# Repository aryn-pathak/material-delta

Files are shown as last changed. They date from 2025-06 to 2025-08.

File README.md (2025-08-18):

# MATERIAL DELTA (stylised as mδ)
## Concept:
**"What if a printer was 3D printed?"** _thats called a reprap printer, nothing new, duh!_

**"Alright, what if it was super cheap, about $150?"** _Impressive, but it's probably super small, super slow, and super low quality too. why not splurge the $350 limit you have!_

**"Nope, what if it was ultra fast too?"** _powerful motors and a 100W hotend, nothing special either-- probably eats up a TON of power!_

**"Can't you ever be happy?! Fine, what if it was powered by USBC?"** _you're kidding thats not possible blah blah blah about how a 3D printer can't be powered by USBC_

The Material DELTA is an opensource delta style 3D printer, built for speed, pockets, and powered by USBC, powered by a RPi Zero 2W running klipper, with raspberry pi pico controlling motors for high speed motion.

## images (they're beautiful)






# BOM:

| Category | Name | Link | Price (INR) | Price (USD) |
|---|---|---|---|---|
| CONTROLLER PARTS | NCE4080K | [Link](https://roboticsdna.in/product/nce4080k-40v-80a-n-channel-enhancement-mode-power-mosfet/) | 108 | 1.296 |
| | PDC004-PD | [Link](https://robu.in/product/pdc004-pd-pd-decoy-module-20v/) | 109 | 1.308 |
| | SMBJ6.0A | [Link](https://roboticsdna.in/product/smbj6-0a-6v-600w-esd-suppressor-tvs-diode-2pin-smb-do-214aa/) | 20 | 0.24 |
| | 100uF 25V Electrolytic Capacitor | [Link](https://robu.in/product/100uf-25v-electrolytic-capacitor-pack-of-10/) | 6 | 0.072 |
| | 1N5819 | [Link](https://roboticsdna.in/product/in5819-schottky-diode/) | 61 | 0.732 |
| | Connector (x2) | [Link](https://roboticsdna.in/product/xy2500-9-pin-3-81-mm-male-pitch-straight-screw-terminal-block-socket/) | 391 | 4.692 |
| | Orpheus Pico | available @ home | 0 | 0 |
| | RPi Zero 2W | available @ home | 0 | 0 |
| | TMC2226 Stepper driver (x4) | [Link](https://novo3d.in/tmc2226-driver/) | 1796 | 21.552 |
| | XL4015 Step down | [Link](https://robu.in/product/xl4015-5a-dc-dc-step-down-adjustable-power-supply-buck-module-led-with-heatsink/) | 75 | 0.9 |
| | XL6019E1 Step up | [Link](https://robu.in/product/xl6019e1-dc-dc-step-converter-performance-ultra-lm2577-booster-circuit-board/) | 155 | 1.86 |
| PRINTER PARTS | Nema 17 (x4) | [Link](https://novo3d.in/42-stepper-motor-nema17/) | 2316 | 27.792 |
| | Volcano heatblock | [Link](https://novo3d.in/pt100-volcano-heat-block/) | 149 | 1.788 |
| | Heater | [Link](https://novo3d.in/24v-50w-heater-cartridge/) | 99 | 1.188 |
| | Heatbreak | [Link](https://novo3d.in/ender3-s1-sprite-throat/) | 169 | 2.028 |
| | CHT Nozzle (0.6mm) | [Link](https://novo3d.in/v6-cht-nozzle/) | 129 | 1.548 |
| | Heatsink | [Link](https://novo3d.in/e3d-v6-heatsink/) | 79 | 0.948 |
| | 3010 Fan | [Link](https://robu.in/product/12v-3010-cooling-fan-for-3d-printer/) | 71 | 0.852 |
| | Pneumatic connector | [Link](https://novo3d.in/pc4-m6/) | 20 | 0.24 |
| | Tube (x2) | [Link](https://novo3d.in/ptfe-tube-white/) | 218 | 2.616 |
| | 2020 extrusions (5m) | [Link](https://www.fastdep.in/product/tslot-2020/?src=search&q=2020) | 1895 | 22.74 |
| | Titan extruder | [Link](https://novo3d.in/titan-extruder/) | 399 | 4.788 |
| | Ball joints for arms | [Link](https://roboticsdna.in/product/reprap-delta-kossel-mini-5347-delta-ball-headed-buckle-ball-caps-parallel-arm-rod-carbon-rod-joints-kit-with-12pcs-m3-for-3d-printer/) | 400 | 4.8 |
| | Carbon fiber arms (x2) | [Link]([https://robu.in/product/pultruded-carbon-fiber-tube-hollow-3mmod-1-5mm-id-1000mm-pack-of-2/](https://robu.in/product/pultruded-carbon-fiber-tube-hollow-6mm-4mm-500mm-pack-of-2/)) | 642 | 7.51 |
| | GT2 timing pulley (x3) | [Link](https://novo3d.in/motor-pulley/) | 75 | 0.9 |
| | Idler pulley | [Link](https://novo3d.in/idler-pulley-6mm/) | 65 | 0.78 |
| | GT2 timing belt | [Link](https://novo3d.in/gt2-6mm-belt/) | 120 | 1.44 |
| | V Slot wheels (x9) | [Link](https://novo3d.in/v-wheel/) | 1071 | 12.852 |
| | 2040 extrusion (3m) | [Link](https://www.fastdep.in/product/tslot-vslot-2040/?src=search&q=2040%2520extrusions) | 2646 | 31.752 |
| | 5010 blower | [Link](https://novo3d.in/blower-cooling-fan-5015/) | 75 | 0.9 |
| | Thermistor | [Link](https://novo3d.in/ntc-sensor/) | 99 | 1.188 |
| | 1kg PLA | [Link](https://novo3d.in/filament/) | 799 | 9.588 |
| | 10mm Spiral Wrapping | [Link](https://robu.in/product/10mm-spiral-wrapping-band-black-10m-for-wires/) | 90 | 1.08 |
| | Round bed sticker | [Link](https://robu.in/product/round-heated-bed-sticker-for-3d-printer-build-plate-with-adhesive-backing/) | 274 | 3.288 |
| | PVC tape | [Link](https://robu.in/product/pro-power-pvc-tape-1920b-general-purpose-tape-pvc-20m-x-19mm/) | 167 | 2.004 |
| | Endstop switches (x6) | [Link](https://roboticsdna.in/product/omron-3d-printer-limit-switch-endstop-ss-5gl/) | 240 | 2.88 |
| FASTENERS | M3 x 12mm | [Link](https://www.fastdep.in/product/socket-head-m3x12mm/) | 26 | 0.312 |
| | M3 x 25mm (x2) | [Link](https://www.fastdep.in/product/socket-head-screws-m3x25mm/) | 60 | 0.72 |
| | M5 x 10mm (x5) | [Link](https://www.fastdep.in/product/socket-head-screws-m5x10mm/) | 140 | 1.68 |
| | M3 Hex Nut | [Link](https://www.fastdep.in/product/hex-nut-m3/) | 18 | 0.216 |
| | M5 hammernut (x50) | [Link](https://novo3d.in/hammernut/) | 300 | 3.6 |
| | M2.5 x 8mm | [Link](https://www.fastdep.in/product/pan-head-screw-m2-5x8mm/) | 48 | 0.576 |
| **TOTAL** | | | **₹15500**  | **$186** |

Huge huge huge thanks to Hack Club and for making this possible :D

# EDITS
- Made new duct, with clearance and pointing right below the nozzle (instead of on it)



- Made it taller for more Z axis
- Added bowden mount for extruder
- Added filament holder



- Modelled in the boards



- Fixed duct based on feedback from reviewers!


- Made new filament holder


- Added belt tensioners!


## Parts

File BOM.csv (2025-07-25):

Category | Name | Link | Price (INR) | Price (USD)
CONTROLLER PARTS | NCE4080K | https://roboticsdna.in/product/nce4080k-40v-80a-n-channel-enhancement-mode-power-mosfet/ | 108 | 1.296
 | PDC004-PD | https://robu.in/product/pdc004-pd-pd-decoy-module-20v/ | 109 | 1.308
 | SMBJ6.0A | https://roboticsdna.in/product/smbj6-0a-6v-600w-esd-suppressor-tvs-diode-2pin-smb-do-214aa/ | 20 | 0.24
 | 100uF 25V Electrolytic Capacitor | https://robu.in/product/100uf-25v-electrolytic-capacitor-pack-of-10/ | 6 | 0.072
 | 1N5819 | https://roboticsdna.in/product/in5819-schottky-diode/ | 61 | 0.732
 | Connector (x2) | https://roboticsdna.in/product/xy2500-9-pin-3-81-mm-male-pitch-straight-screw-terminal-block-socket/ | 391 | 4.692
 | Orpheus Pico | available @ home | 0 | 0
 | RPi Zero 2W | available @ home | 0 | 0
 | TMC2226 Stepper driver (x4) | https://novo3d.in/tmc2226-driver/ | 1796 | 21.552
 | XL4015 Step down | https://robu.in/product/xl4015-5a-dc-dc-step-down-adjustable-power-supply-buck-module-led-with-heatsink/ | 75 | 0.9
 | XL6019E1 Step up | https://robu.in/product/xl6019e1-dc-dc-step-converter-performance-ultra-lm2577-booster-circuit-board/ | 155 | 1.86
PRINTER PARTS | Nema 17 (x4) | https://novo3d.in/42-stepper-motor-nema17/ | 2316 | 27.792
 | Volcano heatblock | https://novo3d.in/pt100-volcano-heat-block/ | 149 | 1.788
 | Heater | https://novo3d.in/24v-50w-heater-cartridge/ | 99 | 1.188
 | Heatbreak | https://novo3d.in/ender3-s1-sprite-throat/ | 169 | 2.028
 | CHT Nozzle (0.6mm) | https://novo3d.in/v6-cht-nozzle/ | 129 | 1.548
 | Heatsink | https://novo3d.in/e3d-v6-heatsink/ | 79 | 0.948
 | 3010 Fan | https://robu.in/product/12v-3010-cooling-fan-for-3d-printer/ | 71 | 0.852
 | Pneumatic connector | https://novo3d.in/pc4-m6/ | 20 | 0.24
 | Tube (x2) | https://novo3d.in/ptfe-tube-white/ | 218 | 2.616
 | 2020 extrusions (5m) | https://www.fastdep.in/product/tslot-2020/?src=search&q=2020 | 1895 | 22.74
 | Titan extruder | https://novo3d.in/titan-extruder/ | 399 | 4.788
 | Ball joints for arms | https://roboticsdna.in/product/reprap-delta-kossel-mini-5347-delta-ball-headed-buckle-ball-caps-parallel-arm-rod-carbon-rod-joints-kit-with-12pcs-m3-for-3d-pr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 | 400 | 4.8
 | Carbon fiber arms (x2) | https://robu.in/product/pultruded-carbon-fiber-tube-hollow-6mm-4mm-500mm-pack-of-2/ | 642 | 7.51
 | GT2 timing pulley (x3) | https://novo3d.in/motor-pulley/ | 75 | 0.9
 | Idler pulley | https://novo3d.in/idler-pulley-6mm/ | 65 | 0.78
 | GT2 timing belt | https://novo3d.in/gt2-6mm-belt/ | 120 | 1.44
 | V Slot wheels (x9) | https://novo3d.in/v-wheel/ | 1071 | 12.852
 | 2040 extrusion (3m) | https://www.fastdep.in/product/tslot-vslot-2040/?src=search&q=2040%2520extrusions | 2646 | 31.752
 | 5010 blower | https://novo3d.in/blower-cooling-fan-5015/ | 75 | 0.9
 | Thermistor | https://novo3d.in/ntc-sensor/ | 99 | 1.188
 | 1kg PLA | https://novo3d.in/filament/ | 799 | 9.588
 | 10mm Spiral Wrapping | https://robu.in/product/10mm-spiral-wrapping-band-black-10m-for-wires/ | 90 | 1.08
 | Round bed sticker | https://robu.in/product/round-heated-bed-sticker-for-3d-printer-build-plate-with-adhesive-backing/ | 274 | 3.288
 | PVC tape | https://robu.in/product/pro-power-pvc-tape-1920b-general-purpose-tape-pvc-20m-x-19mm/ | 167 | 2.004
 | Endstop switches (x6) | https://roboticsdna.in/product/omron-3d-printer-limit-switch-endstop-ss-5gl/ | 240 | 2.88
FASTENERS | M3 x 12mm | https://www.fastdep.in/product/socket-head-m3x12mm/ | 26 | 0.312
 | M3 x 25mm (x2) | https://www.fastdep.in/product/socket-head-screws-m3x25mm/ | 60 | 0.72
 | M5 x 10mm (x5) | https://www.fastdep.in/product/socket-head-screws-m5x10mm/ | 140 | 1.68
 | M3 Hex Nut | https://www.fastdep.in/product/hex-nut-m3/ | 18 | 0.216
 | M5 hammernut (x50) | https://novo3d.in/hammernut/ | 300 | 3.6
 | M2.5 x 8mm | https://www.fastdep.in/product/pan-head-screw-m2-5x8mm/ | 48 | 0.576
TOTAL |  |  | ₹15500 | $186

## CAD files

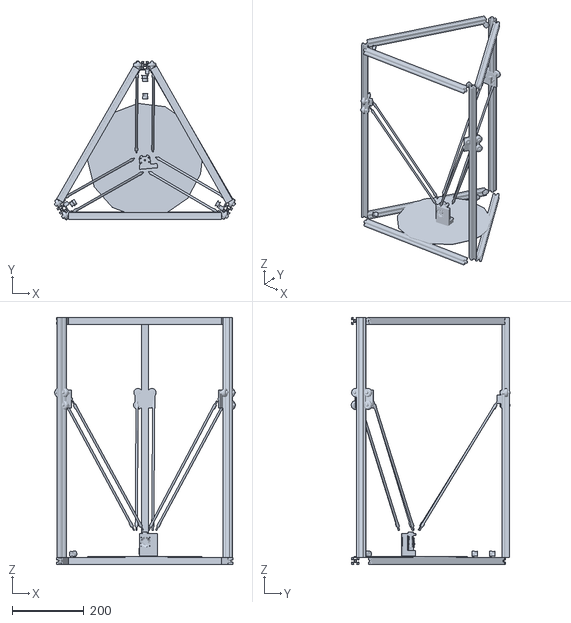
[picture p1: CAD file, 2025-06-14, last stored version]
Material DELTA assembly.stl
506.2 x 443.3 x 690.0

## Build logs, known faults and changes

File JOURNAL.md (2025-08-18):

Made by: @aryan

Repository link: https://github.com/aryn-pathak/material-zero/ 

TOTAL TIME (source screentime): ~36 Hours (and 40 hours on old printer)

---

title: "Material DELTA"
author: "aryan pathak"
description: "A Delta style printer, powered by USB-C"
created_at: "2025-06-02"

---

Massive thanks to Hack Club and Alex for giving me this insane opportunity to build my own 3D printer!

This is Material DELTA, An open source, superfast, super cheap, (most importantly) USBC powered, Delta-style 3D printer.

## DAY ONE
My old printer wasn't for a long time since i submitted it on 7th of april, but that gave me time to realise that it wasn't good. It was unnecesarily expensive, structure was unstable and probably slow, the printer was very average and didn't have any big innovative feature (just hands free printing powered by an RPi and a web server)
Post some research, I came across a much more uncommon kinematic of 3D printers-- Delta. One of the goals of my old printer (that I realised was beyond unrealistic), was powering it with USBC. A delta printer meant there would be so little load on each motor, current draw would be very minimal.

This is what my old printer design looked like:
Old printer

A solid plan with me, I know I am 100% going to build this.

## DAY TWO - FOUR
I started building the printer. Everything was going very very well. Costs were minimal. I found out that carbon fiber rods were used for the lightweight arms of the printer, but i got a bit carried away, and built the entire printer's frame out of carbon fiber :sob:
I made the carriage too, which would have ball joints (3D printed, and a 8mm ball glued on)

#### CAD and research: ~6 hours

## DAY FIVE-SIX
Wasted a ton of time on making the top and bottom holders (out of carbon fiber too), and with 3D printed holders (very very unstable and inconsistent). Making them took a LOT of time because i was trying to make an equilateral triangle and trying to adjust the rods and the holders and everything, which took 2 days sadly

Corner holders:

these weren't practical or accurate at all, but this is what it looked like

#### CAD: ~4.5-5 hours

## DAY SEVEN-EIGHT
Did some chatGPT-ing for design ideas, and also realised carbon fiber rods were insanely impractical and unstable, so i decided to make the frame out of 2020 AND 2040 extrusions. Also found something called "Kossel-style corners" which are 3D printed holders for the frame
kossel corners



I also designed the carriage today:



#### CAD, bit of ChatGPT: ~4.5-5 hours

## DAY NINE
EXTRUDER SHOPPING !! im using a bowden setup, and all hotends are either more expensive than my entire printer or slow and generic. My custom hotend assembly would be made of a V6 heatsink, 65W heat cartridge (not the best, ik, but it fits in my power budget of 100W for USBC), a volcano style heatblock, CHT 0.4mm nozzle, and a bimetal heatbreak.

Volcano heatblock (slightly different from V6, provides better heat retention (needed for low wattage heater):

Screenshot 2025-06-28 at 4 14 47 PM

CHT nozzle with 3 holes for better melting efficiency:

Screenshot 2025-06-28 at 4 18 40 PM

#### Shopping and research: ~2.5-3 hours

## DAY TEN
Curated the BOM, currently, the printer costs about 100USD (1/3rd of the max budget). (remind me to keep making the BOM alongside the printer design process :sob:). Also, i've decided that for the printer, I won't be using a motherboard, but use an RPi Zero (which i have at home) giving it wireless capabilities, running Klipper. But a bit of research revealed that it's GPIO isn't fast enough, and thankfully I also had an orph Pico from highseas lying around, which is much more suitable for swiftly controlling motors.

#### MORE RESEARCH: ~2 hours

## DAY ELEVEN-FOURTEEN
Wasted a ton of time again, this time for designing the effector (the hotend carrier). I had to design a duct for the 5015 blower too, and made 3-4 iterations of it, but finally settled on a super simple duct and overall design, and also looks great.
I even found a set of 12 threaded balls and sockets (called 5347 rod ends), which was really helpful since the 3D printed ones wouldnt give a lot of freedom of movement.
Screenshot 2025-06-28 at 4 20 42 PM

I also found out that these are for 3mm rods, so i had to design an adapter for my 6mm rods:


#### mostly CAD: ~9.5-10 hours

## DAY FIFTEEN
I'll try to submit the printer finally today, so the documentation, logs, final BOM, including the most important parts-- USBC PD negotiation board and all the small parts needed to make it work, like buck converters, boosters, etc. finishing touches-- I'll get all that done today and submit it :D

This is a USB-C-PD Decoy board, which negotiates PD (upto 100W) with the power source.
Screenshot 2025-06-28 at 4 46 29 PM

## DAY SIXTEEN-SEVENTEEN
Worked on BOM, finishing touches here and there, and finally submitting it after 40+36 hours 😭

#### finishing touches, research, shopping: ~2.5-3 hours

here are some images for you :)




# BOM:
| Category | Name | Link | Price (INR) | Price (USD) |
|---|---|---|---|---|
| CONTROLLER PARTS | NCE4080K | [Link](https://roboticsdna.in/product/nce4080k-40v-80a-n-channel-enhancement-mode-power-mosfet/) | 108 | 1.296 |
| | PDC004-PD | [Link](https://robu.in/product/pdc004-pd-pd-decoy-module-20v/) | 109 | 1.308 |
| | SMBJ6.0A | [Link](https://roboticsdna.in/product/smbj6-0a-6v-600w-esd-suppressor-tvs-diode-2pin-smb-do-214aa/) | 20 | 0.24 |
| | 100uF 25V Electrolytic Capacitor | [Link](https://robu.in/product/100uf-25v-electrolytic-capacitor-pack-of-10/) | 6 | 0.072 |
| | 1N5819 | [Link](https://roboticsdna.in/product/in5819-schottky-diode/) | 61 | 0.732 |
| | Connector (x2) | [Link](https://roboticsdna.in/product/xy2500-9-pin-3-81-mm-male-pitch-straight-screw-terminal-block-socket/) | 391 | 4.692 |
| | Orpheus Pico | available @ home | 0 | 0 |
| | RPi Zero 2W | available @ home | 0 | 0 |
| | TMC2226 Stepper driver (x4) | [Link](https://novo3d.in/tmc2226-driver/) | 1796 | 21.552 |
| | XL4015 Step down | [Link](https://robu.in/product/xl4015-5a-dc-dc-step-down-adjustable-power-supply-buck-module-led-with-heatsink/) | 75 | 0.9 |
| | XL6019E1 Step up | [Link](https://robu.in/product/xl6019e1-dc-dc-step-converter-performance-ultra-lm2577-booster-circuit-board/) | 155 | 1.86 |
| PRINTER PARTS | Nema 17 (x4) | [Link](https://novo3d.in/42-stepper-motor-nema17/) | 2316 | 27.792 |
| | Volcano heatblock | [Link](https://novo3d.in/pt100-volcano-heat-block/) | 149 | 1.788 |
| | Heater | [Link](https://novo3d.in/24v-50w-heater-cartridge/) | 99 | 1.188 |
| | Heatbreak | [Link](https://novo3d.in/ender3-s1-sprite-throat/) | 169 | 2.028 |
| | CHT Nozzle (0.6mm) | [Link](https://novo3d.in/v6-cht-nozzle/) | 129 | 1.548 |
| | Heatsink | [Link](https://novo3d.in/e3d-v6-heatsink/) | 79 | 0.948 |
| | 3010 Fan | [Link](https://robu.in/product/12v-3010-cooling-fan-for-3d-printer/) | 71 | 0.852 |
| | Pneumatic connector | [Link](https://novo3d.in/pc4-m6/) | 20 | 0.24 |
| | Tube (x2) | [Link](https://novo3d.in/ptfe-tube-white/) | 218 | 2.616 |
| | 2020 extrusions (5m) | [Link](https://www.fastdep.in/product/tslot-2020/?src=search&q=2020) | 1895 | 22.74 |
| | Titan extruder | [Link](https://novo3d.in/titan-extruder/) | 399 | 4.788 |
| | Ball joints for arms | [Link](https://roboticsdna.in/product/reprap-delta-kossel-mini-5347-delta-ball-headed-buckle-ball-caps-parallel-arm-rod-carbon-rod-joints-kit-with-12pcs-m3-for-3d-printer/) | 400 | 4.8 |
| | Carbon fiber arms (x2) | [Link]([https://robu.in/product/pultruded-carbon-fiber-tube-hollow-3mmod-1-5mm-id-1000mm-pack-of-2/](https://robu.in/product/pultruded-carbon-fiber-tube-hollow-6mm-4mm-500mm-pack-of-2/)) | 642 | 7.51 |
| | GT2 timing pulley (x3) | [Link](https://novo3d.in/motor-pulley/) | 75 | 0.9 |
| | Idler pulley | [Link](https://novo3d.in/idler-pulley-6mm/) | 65 | 0.78 |
| | GT2 timing belt | [Link](https://novo3d.in/gt2-6mm-belt/) | 120 | 1.44 |
| | V Slot wheels (x9) | [Link](https://novo3d.in/v-wheel/) | 1071 | 12.852 |
| | 2040 extrusion (3m) | [Link](https://www.fastdep.in/product/tslot-vslot-2040/?src=search&q=2040%2520extrusions) | 2646 | 31.752 |
| | 5010 blower | [Link](https://novo3d.in/blower-cooling-fan-5015/) | 75 | 0.9 |
| | Thermistor | [Link](https://novo3d.in/ntc-sensor/) | 99 | 1.188 |
| | 1kg PLA | [Link](https://novo3d.in/filament/) | 799 | 9.588 |
| | 10mm Spiral Wrapping | [Link](https://robu.in/product/10mm-spiral-wrapping-band-black-10m-for-wires/) | 90 | 1.08 |
| | Round bed sticker | [Link](https://robu.in/product/round-heated-bed-sticker-for-3d-printer-build-plate-with-adhesive-backing/) | 274 | 3.288 |
| | PVC tape | [Link](https://robu.in/product/pro-power-pvc-tape-1920b-general-purpose-tape-pvc-20m-x-19mm/) | 167 | 2.004 |
| | Endstop switches (x6) | [Link](https://roboticsdna.in/product/omron-3d-printer-limit-switch-endstop-ss-5gl/) | 240 | 2.88 |
| FASTENERS | M3 x 12mm | [Link](https://www.fastdep.in/product/socket-head-m3x12mm/) | 26 | 0.312 |
| | M3 x 25mm (x2) | [Link](https://www.fastdep.in/product/socket-head-screws-m3x25mm/) | 60 | 0.72 |
| | M5 x 10mm (x5) | [Link](https://www.fastdep.in/product/socket-head-screws-m5x10mm/) | 140 | 1.68 |
| | M3 Hex Nut | [Link](https://www.fastdep.in/product/hex-nut-m3/) | 18 | 0.216 |
| | M5 hammernut (x50) | [Link](https://novo3d.in/hammernut/) | 300 | 3.6 |
| | M2.5 x 8mm | [Link](https://www.fastdep.in/product/pan-head-screw-m2-5x8mm/) | 48 | 0.576 |
| **TOTAL** | | | **₹15500**  | **$186** |

## NOTE: Aluminium print bed is fixed to extrusions using screws. Will be sut and drilled at a local shop

# EDITS AFTER SUBMISSION 

- Made new duct, with clearance and pointing right below the nozzle (instead of on it)



- Made it taller for more Z axis
- Added bowden mount for extruder
- Added filament holder



- Modelled in the boards



# MORE EDITS AFTER SUBMISSION
- Fixed duct based on feedback from reviewers!


- Made new filament holder


- Added belt tensioners!


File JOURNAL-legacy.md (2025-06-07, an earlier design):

Made by: @aryan
Repository link: https://github.com/aryn-pathak/material-zero/
Total hours so far: 39.5 Hours (wished i worked 30 mins more to hit 40 :heavysob:)

Massive thanks to Hack Club and Alex for giving me this insane opportunity to build my own 3D printer!

This is Material ZERO (zero for being the zero-th version of a printer that will be heavily modified to make better versions down the line.), A printer that is easy to modify, upgrade, and most importantly-- to use.
- Features a truly hands free experience for printing; simply uploading an stl file on the web interface and choosing a preset (fast, hi-res, fast with supports, or hi-res with supports). That's it: slicing, supports, settings, ABL, all handled by Material.
- The printer also features a magnetic printhead (with wiring!), so swapping out toolheads is just a click of neodyium magnets away!

- [x] I have access to a 3D printer (printing-leigon)

BOM: https://docs.google.com/spreadsheets/d/1OtqszPI16ybW3s_6Pz4gcUsUTPw2b_rEn2WlHAjkEtA/

**NOTE: THE ENTIRE PRINTER WAS REBUILT AFTER A REALISATION MUCH LATER, WITH A COMPLETELY NEW CONCEPT. THE FOLLOWING LOG FOLLOWS THE DEVELOPMENT OF THE OLD ONE (LEGACY)**

--OLD LOG--
## DAY ONE // 18th March
- I'm new to this so I did a ton of research today :D. I have gained an understanding of mechanisms, and feel much more confident now!
- Research time: 1 hour

## DAY TWO // 19th March
- Curated the BOM today, and I have a vision of what I want my printer to have:
- ~~Should have USBC, Portable, size perhaps 55 x 55 x 55, Battery powered (obvio). Preferably but not compulsorily wireless~~
- ~~Since this is going to be portable, the hotbed should have a firmer grip.~~ I would've loved these features but it'd be hella impractical and slow and inefficient 
Time spent: approximately. 30 mins

## DAY THREE // 21st March
- I need to lock in for the next ten days now.
- Im making the BOM in google docs now, and the parts I found out earlier are now out of stock/very low stock, so I'll make a BOM from novo3d.in
- Also, I have decided to make a slightly different kind of printer, new requirements:
    - ~~USBC~~, WiFi/BLE compatibility
    - Should be fast
    - It should continue printing right where it left off in case of power outage
    - Should have a camera and software to create good timelapses
    - It will also have a grid of neopixels to indicate the progress
    - It will have a touch display which can show contols, progress (in time) and estimated time remaining.
    - The camera should be able to stream the progess if requested by user wirelessly.
 
- Time spent: 30 mins

## DAY FOUR // 22nd March
- Got a lot of progress on the BOM, now I can start working on CAD
- I need to watch a tutorial on FreeCAD
- I also got another insane idea: what if the printer could make filament out of random plastic pieces? (note from future: will add this feature through a custom printhead/bottle cutter filament thing that I'll print with my printer)
- Time spent: 2.5 hours

## DAY FIVE // 23rd March 
- Yesterday night, while racking my brain, I decided to make a bedslinger instead of X and Y axes being controlled by the printhead.
- X and Z axes will be controlled by the printhead, Y will be controlled by the heatbed. 
- X and Y to be controlled with belt and Z will be controlled by lead screws.
- Another idea: I have found a yt video to directly print plastic shreds instead of making filament first. For this, the printhead has an extension on top of it (like a hat).
- However this modified printhead will not be able to print filament. To solve this problem, I will have two printheads, which can be swapped magnetically.
- The bracket which is controlled by the belt will have neodymium magnets embedded. the swappable printheads too will have magnets embedded.

- I found this resource: https://www.instructables.com/DIY-3D-Printer-From-Scratch/ which has helped me a TON! Everything just got a who lot easier, because I had so many misconceptions regarding the structure and mechanisms.
- I will be ditching the linear rails entirely and use smooth rods.
- Also, my old bracket for the belt was supposed to be attached to the belt using grooves, but watching a video, I can just attach it using a ziptie.
- Also, I will now be using open belts instead of closed ones, which is a good thing, because I couldn't find an appropriate size for the belt.

- Finally got started on CAD today, (only started tho 😬)
- Need to get much much more productive tommorow 

Time spent today: 2 hours (was planning on 5 tho)

DAY SIX // 24th March
- I was quite productive today, much progress on CAD (completed X and Z axes):

X and Z axes

- I'm hoping I can complete the Y axis aswell, and then complete the printhead and heatbed tommorow, but I have homework to do :heavysob:

- Sadly I wasn't able to continue any work after this, but I will make some sketches tonight for the Y axis, and maybe of the structure too.

- I'm also thinking of making my own motherboard, as it gives me full freedom, however, I'll have to research before I can commit to it. (I also wanted to make my own firmware but I figured time isn't on my side and it's overkill)

- Also, here are some of my sketches of old and new designs so far:
sketch1
sketch2
sketch3

I love how messy they look :D

CAD: 3 hours

DAY SEVEN // 25th March
- I got straight into PCB design for the motherboard, but I'm reconsidering now, maybe I don't need to make my own motherboard.
- If I'm done with the entire thing and still have time left, I'll start working on it.
- Also, some research revealed I can't use USBC to power the printer D:
- Quite some progress today, worked on Y axis (all 3 axes successfully done)
- I can get to making the printhead and structure tommorow.
- If I have time, I'll make my own motherboard with an rpi zero W as the controller (I have some)

Here's the CAD till now:
CAD

CAD2

Research: 2 hours, CAD: 2 hours.

DAY EIGHT // 26 March
(logging on 27th March)

- Couldn't get much work done today, but did some research and found a nice midrange motherboard and found a great extruder kit (Titan kit) for quite cheap!
titan extruder kit
titan extruder kit
research: ~45 minutes

DAY NINE // 27 March

- Finished frame today :D (fixed a lot of errors in the model too)
- Researched a bit too
- Had some progress today, but not nearly as much as I had planned :heavysob:

research: 45 minutes 
CAD: 2 hours

DAY TEN // 28 March

- Refined the frame today, built the magnetic toolhead and the adapter for my titan extruder!!
toolhead
toolhead
toolhead
- Completely finished with my printer... or so i thought 
printer
- I talked to some people on slack and research a bit (a lot), and I'm gonna use extrusions for the frame.
- Luckily I found some mounts on novo3d which fit perfectly with the 2040 profile extrusions.
- I started working on the new frame, but I'll do the rest tommorow.

Research: 2.5 hours (approx)
CAD: 2.5 hours

DAY ELEVEN // 29 March
- Made progress on the Y axis using extrusions, but I need to figure out how to connect the belt to my heatbed. Gonna use Gantry beds instead of rods for the Y axis.
- Also made a bracket to connect the Z axis to the extrusions.
- Much less progress than I hoped for, but I'll finish the printer by tommorow most likely.

CAD + some research: 2 hours 25 minutes

DAY TWELVE // 30 March 
- Completed the printer with extrusions today :D
- I'll use the remaining days to work on finishing touches and adding features.
- Didn't get research done today since I was traveling tho

printer

CAD: 3 hours 

DAY THIRTEEN // 31 March
- Today is mostly for research and implementing special features.
- For now, scratch the vision for my printer I had mentioned before, for now, the printer will have the following features:
    - Hands free printing: I want to build a printer that requires minimal human input and contact with the printer. I will connect a raspberry pi zero to the motherboard to add more features and use a web interface for starting prints automatically.
    - I also don't want to spend too much time fiddling with the print settings everytime I need to print something. I want to just plug it in, upload a file (remotely), and boom- all the settings will be configured by algorithms on the raspberry pi and the print will start.

DAY FOURTEEN // 6 April
- Worked on software only today
- The printer will be equipped with software for truly hands-free operation, which means the user just has to upload the STL file, which gets stored, sliced, with supports (if required).
- This will mean that a raspberry Pi will be connected to the btt e3 mini acting as the computer uploading the file. The firmware is in a very early age, and will get a lot of features later on yay

Code: 1 hour

DAY FIFTEEN // 7 April
- Pure CAD today. Absolutely nothing else.
- The deadline's closing in, and luckily because of my time zone (IST), this ends on 9:30AM on 8th april, so I'll make the PCB and code and the last bits of CAD early tommorow 🤞

CAD: 4 hours

DAY SIXTEEN // 8 April
- DONEDONEDONEDONEDONEDONE
- (woke up at 5:30, skipped school, finished the printer by 10AM)
- Finished CAD, Finished software, Compiled BOM (along with screws!)

CAD: 1.5h
Research, BOM, etc: 2h
Coding: 45 mins
(screentime shows music: 1h 45mins...?)
total: 4.5 hours

printer
printer
printer
printer

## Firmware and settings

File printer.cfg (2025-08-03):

[mcu]
serial: /dev/serial/by-id/usb-Klipper_rp2040_xxxxx-if00
restart_method: command

[printer]
kinematics: delta
max_velocity: 200
max_accel: 2000
max_z_velocity: 120
max_z_accel: 1000
min_position: -155,-155,0
max_position: 155,155,420
delta_radius: 270.0
delta_tower_angle_a: 210
delta_tower_angle_b: 330
delta_tower_angle_c: 90

[stepper_a]
step_pin: gpio0
dir_pin: gpio1
enable_pin: !gpio2
microsteps: 16
rotation_distance: 40
endstop_pin: ^gpio3
position_endstop: 0.0
arm_length: 390.0

[stepper_b]
step_pin: gpio4
dir_pin: gpio5
enable_pin: !gpio6
microsteps: 16
rotation_distance: 40
endstop_pin: ^gpio7
position_endstop: 0.0
arm_length: 390.0

[stepper_c]
step_pin: gpio8
dir_pin: gpio9
enable_pin: !gpio10
microsteps: 16
rotation_distance: 40
endstop_pin: ^gpio11
position_endstop: 0.0
arm_length: 390.0

[delta_calibrate]
radius: 270.0

[extruder]
step_pin: gpio12
dir_pin: gpio13
enable_pin: !gpio14
microsteps: 16
rotation_distance: 7.5
nozzle_diameter: 0.6
filament_diameter: 1.75
heater_pin: gpio15
sensor_type: NTC 100K beta=3950
sensor_pin: gpio26
min_temp: 0
max_temp: 220
max_extrude_only_distance: 100.0
control: pid

[fan]
pin: gpio16

[tmc2226 stepper_a]
uart_pin: gpio17
run_current: 0.9
hold_current: 0.5

[tmc2226 stepper_b]
uart_pin: gpio18
run_current: 0.9
hold_current: 0.5

[tmc2226 stepper_c]
uart_pin: gpio19
run_current: 0.9
hold_current: 0.5

[tmc2226 extruder]
uart_pin: gpio20
run_current: 0.8
hold_current: 0.4

[delta_tower_angle_trims]
tower_a_angle: 0
tower_b_angle: 0
tower_c_angle: 0

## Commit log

2025-06-14 Create printer assembly
2025-06-14 Update printer assembly
